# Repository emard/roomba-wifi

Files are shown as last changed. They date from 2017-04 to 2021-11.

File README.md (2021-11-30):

# WiFi-Roomba: ESP8266 Nodemcu interface for iRobot Roomba

Wifi remote control interface for the iRobot Roomba vacuum cleaner.
Tested on model 880, others 600-900 have similar command
set and probably will work too.

telnet to roomba IP while it is charging, it should display something like this:

    telnet 192.168.0.2
    Trying 192.168.0.2...
    Connected to 192.168.0.2.
    Escape character is '^]'.
    bat:   min 0  sec 10  mV 17061  mA 1016  tenths-deg-C 348  mAH 2696  state 5  
    bat:   min 0  sec 11  mV 17061  mA 1016  tenths-deg-C 348  mAH 2696  state 5  
    bat:   min 0  sec 12  mV 17061  mA 1008  tenths-deg-C 348  mAH 2696  state 5  
    bat:   min 0  sec 13  mV 17061  mA 1023  tenths-deg-C 348  mAH 2696  state 5  

To reset roomba to similar state like battery was replaced,
type CTRL-G and ENTER. Roomba beeps and prints different
messages after reset and again battery charging messages as above.

to exit telnet, type CTRL-] quit ENTER

    ^]
    telnet> quit

python3 script to send "DOCK" command

    #!/usr/bin/env python3
    import socket
    s = socket.socket(socket.AF_INET, socket.SOCK_STREAM)
    s.connect(("192.168.0.2",23))
    #print(s.recv(256))
    #s.send(bytearray([128, 135, 173])) # start, clean, stop
    s.send(bytearray([128, 143, 173])) # start, seek dock, stop
    s.close()

python3 script to shown 4 chars approximated on 7-segment display:

    #!/usr/bin/env python3
    import socket, sys, time
    disp = sys.argv[1][0:4].encode() # max 4 chars
    disp += b" " * (4-len(disp)) # pad length 4 with spaces
    s = socket.socket(socket.AF_INET, socket.SOCK_STREAM)
    s.connect(("192.168.48.116",23))
    s.send(bytearray([128, 131, 174])) # safe mode
    time.sleep(0.05)
    s.send(bytearray([164])+disp)
    s.close()

    ./roomba.disp.py TEST

Other commands are described in
[iRobot Roomba 600 Open Interface Spec](https://www.irobotweb.com/-/media/MainSite/PDFs/About/STEM/Create/iRobot_Roomba_600_Open_Interface_Spec.pdf)

# Wifi Module

Get nodemcu from ebay for $3.5 and flash it with some TCP-serial
bridge code.

From Arduino install ESP8266 support from Boards Manager.

set board to "NodeMCU 1.0 (ESP-12E Module)".

open Examples -> ESP8266Wifi ->  WifiTelnetToSerial

setup WiFi user and password to connect to local access 
point and enable "SWAP_PINS" to use hardware serial 115200,8,n,1
connected as RX=gpio13, TX=gpio15 to Roomba:

    #define SWAP_PINS 1

To compile and write flash, click round blue button with right arrow.

When monitored at USB-serial port, it will print IP address where it
connected.

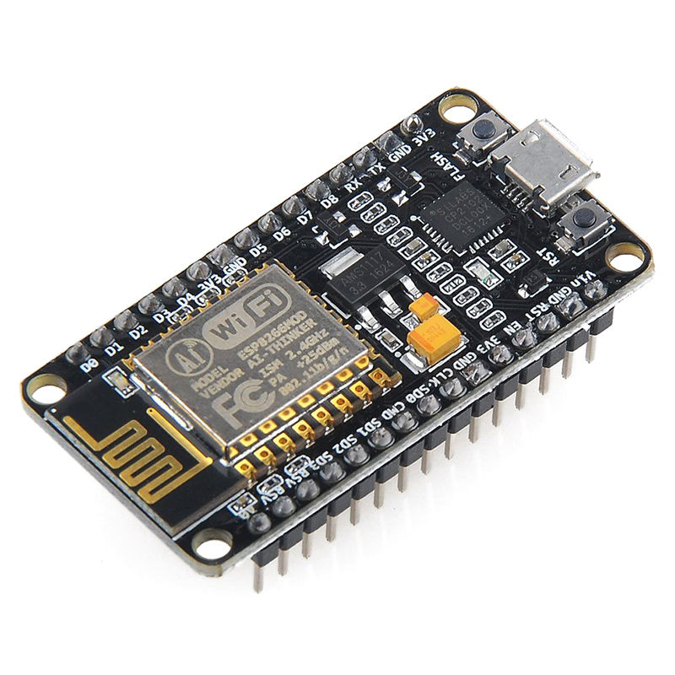
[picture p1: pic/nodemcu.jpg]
nodemcu


# Power supply

Get 3.3V switching power supply module from ebay for $2:

    2A DC 5V-23V to 3.3V DC-DC Step-Down Power Supply Buck Module for esp8266 WiFi

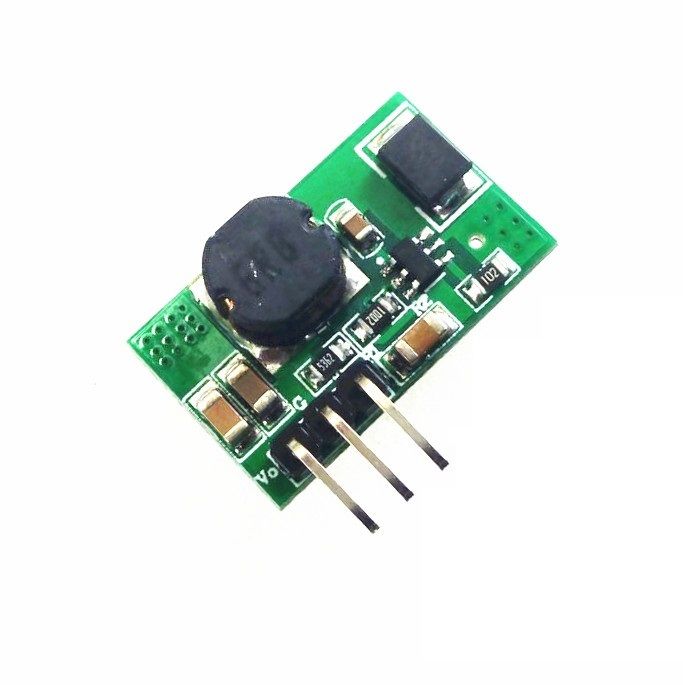
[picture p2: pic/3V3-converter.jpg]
3.3V converter


On the back of the module PCB is written:

       Canton-Power
          DC-DC
    Step-Down Converter
    3.3V[x] 5V[ ] Vi GND Vo

# Cable

Adafruit has roomba cable.
Also apple or mac 8-pin mini-din cable ordered from ebay
will fit to roomba socket (it has extra middle pin which
is NC in roomba socket).

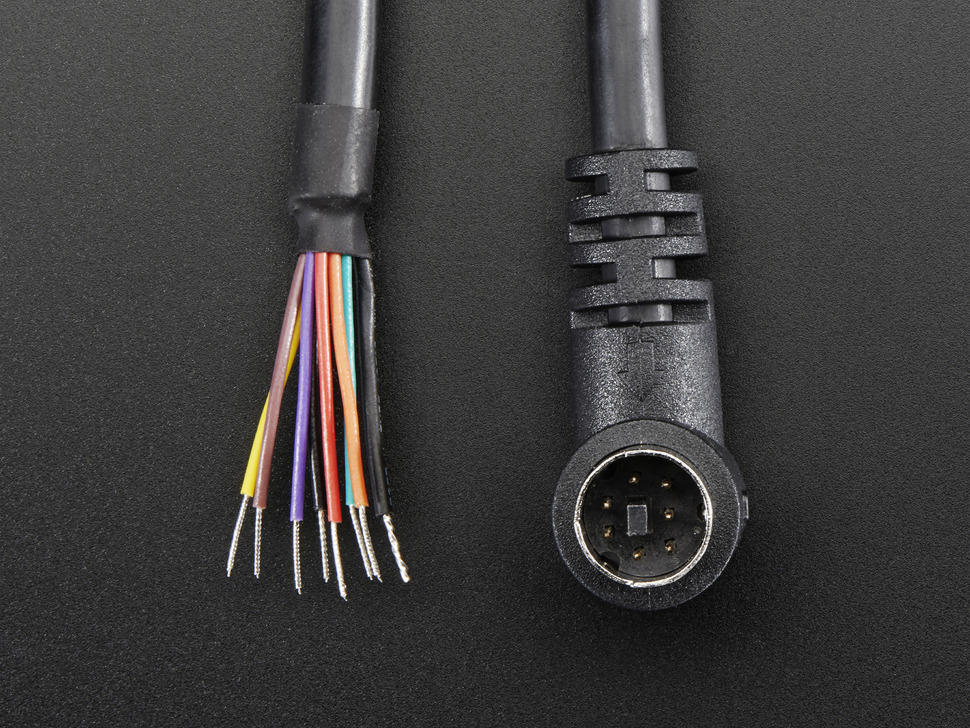
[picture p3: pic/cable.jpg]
cable


pinout (wire colors inside of apple cable)

    1  Vpwr   red    ? no voltage
    2  Vpwr   brown  20V
    3  RXD    orange input to roomba 5V TTL <- wifi_gpio15
    4  TXD    black  output from roomba 5V TTL -> wifi_gpio13
    5  DD     yellow wifi_gpio12
    6  GND    green
    7  GND    blue
    8  NC     violet (middle pin)
    SHIELD    naked

same pin numbering to DB9 connector

# PCB

You can order from OSHpark, seeedstudio or similar, email them gerber
files and they will send back the PCB:

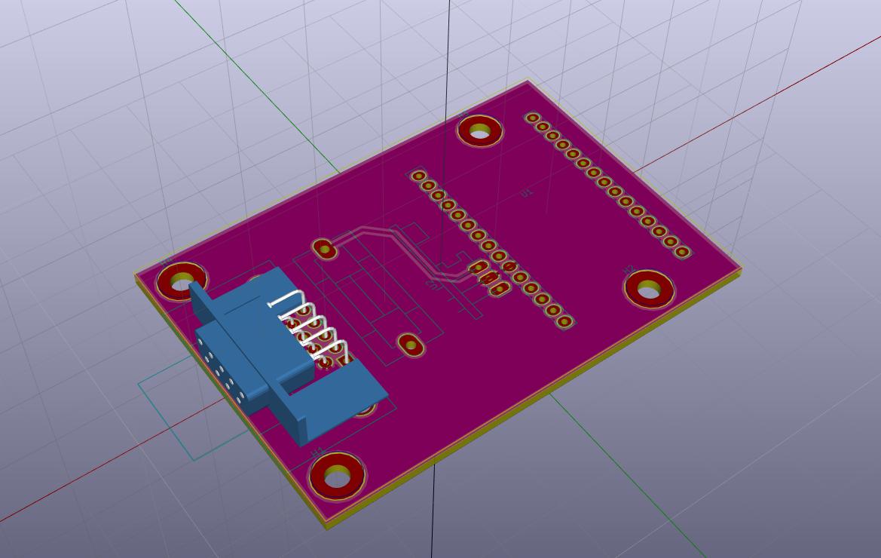
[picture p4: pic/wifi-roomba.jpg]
pcb


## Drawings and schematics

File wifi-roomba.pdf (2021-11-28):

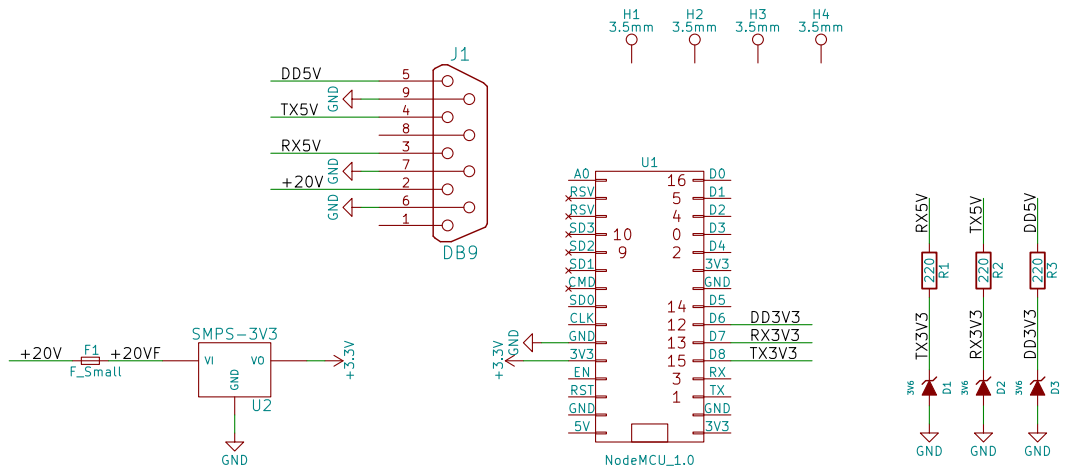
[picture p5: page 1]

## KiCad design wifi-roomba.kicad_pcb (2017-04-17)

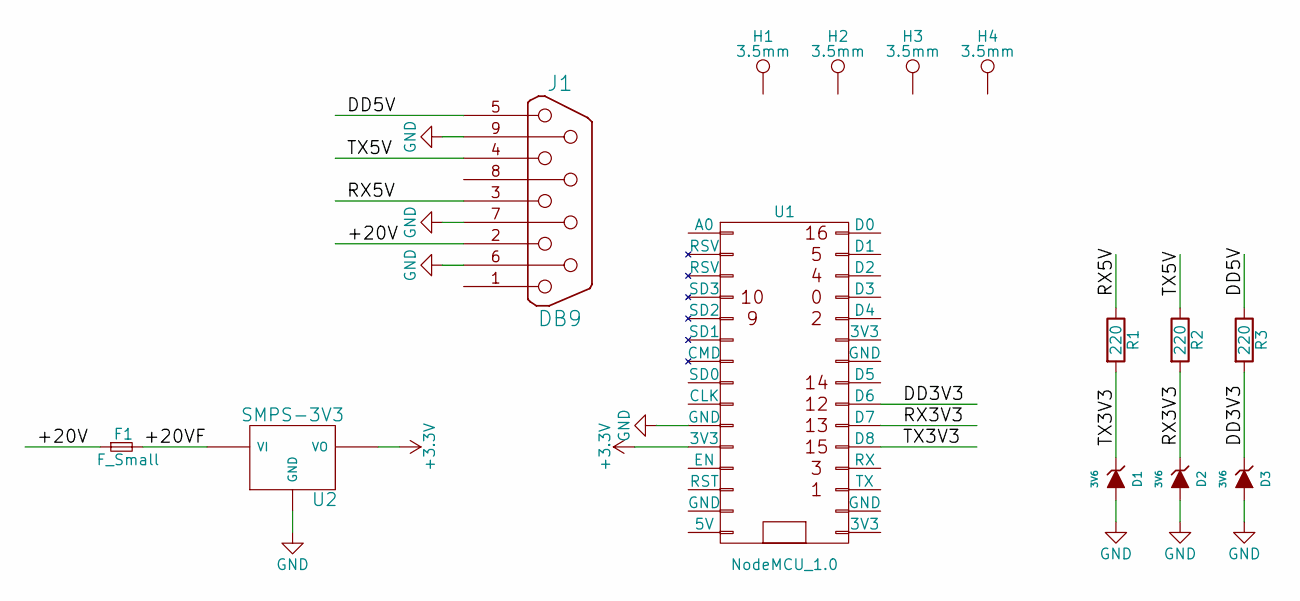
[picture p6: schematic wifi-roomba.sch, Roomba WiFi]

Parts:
D1, D2, D3: 3V6; SMD-1206_Pol
F1: F_Small; Fuseholder5x20_horiz_SemiClosed_Casing10x25mm
H1, H2, H3, H4: 3.5mm; MountingHole_3.5mm_Pad
J1: DB9; DB9FC
R1, R2, R3: 220; R_1206
U1: NodeMCU_1.0
U2: SMPS-3V3; PINHEAD1-3

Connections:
+3V3: U1.11 (3V3), U2.VO
/+20V: F1.1, J1.2
/+20VF: F1.2, U2.VI
/DD3V3: D3.1 (K), R3.2, U1.22 (D6)
/DD5V: J1.5, R3.1
/RX3V3: D2.1 (K), R2.2, U1.21 (D7)
/RX5V: J1.3, R1.1
/TX3V3: D1.1 (K), R1.2, U1.20 (D8)
/TX5V: J1.4, R2.1
GND: D1.2 (A), D2.2 (A), D3.2 (A), J1.6, J1.7, J1.9, U1.10 (GND), U2.GND

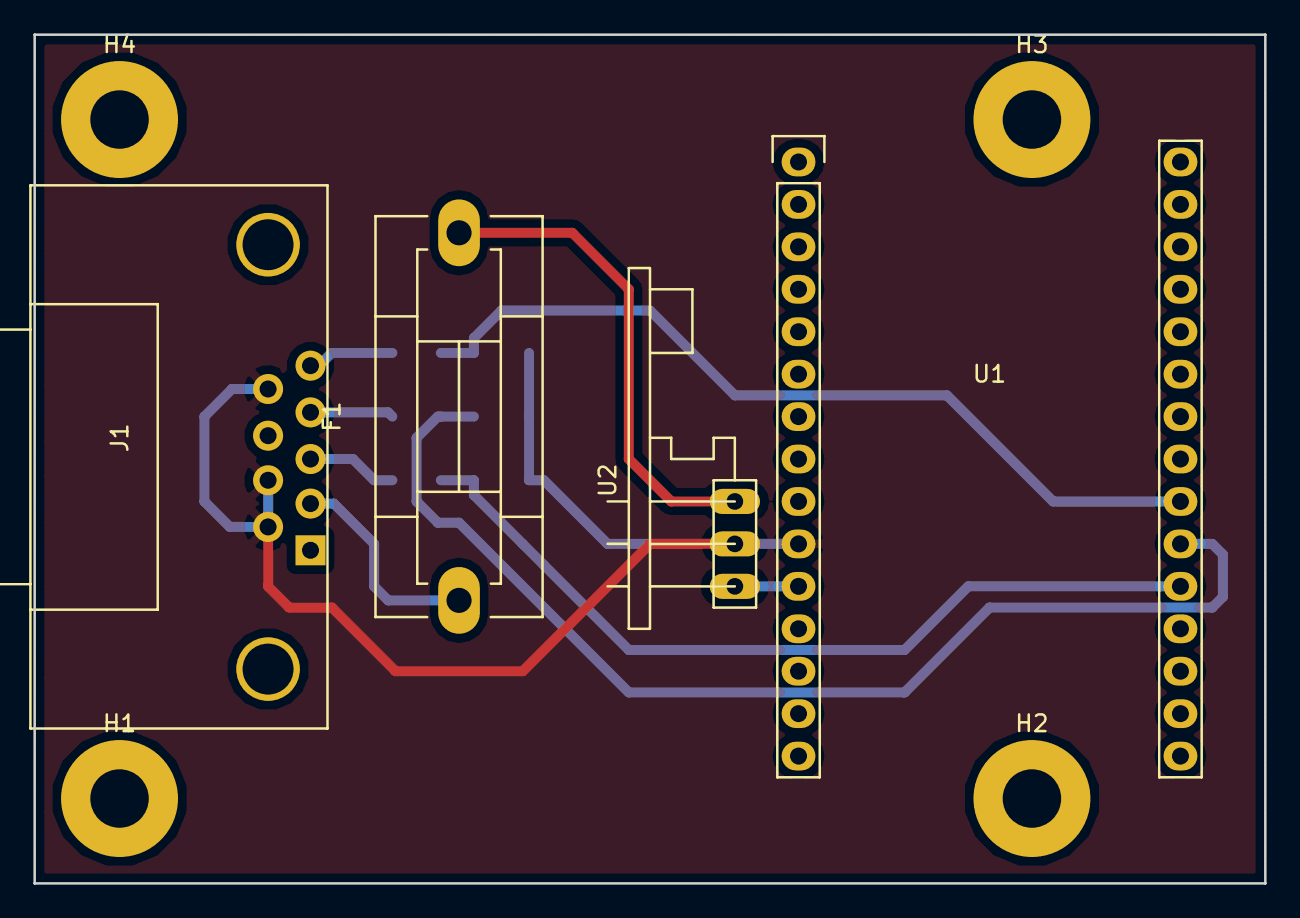
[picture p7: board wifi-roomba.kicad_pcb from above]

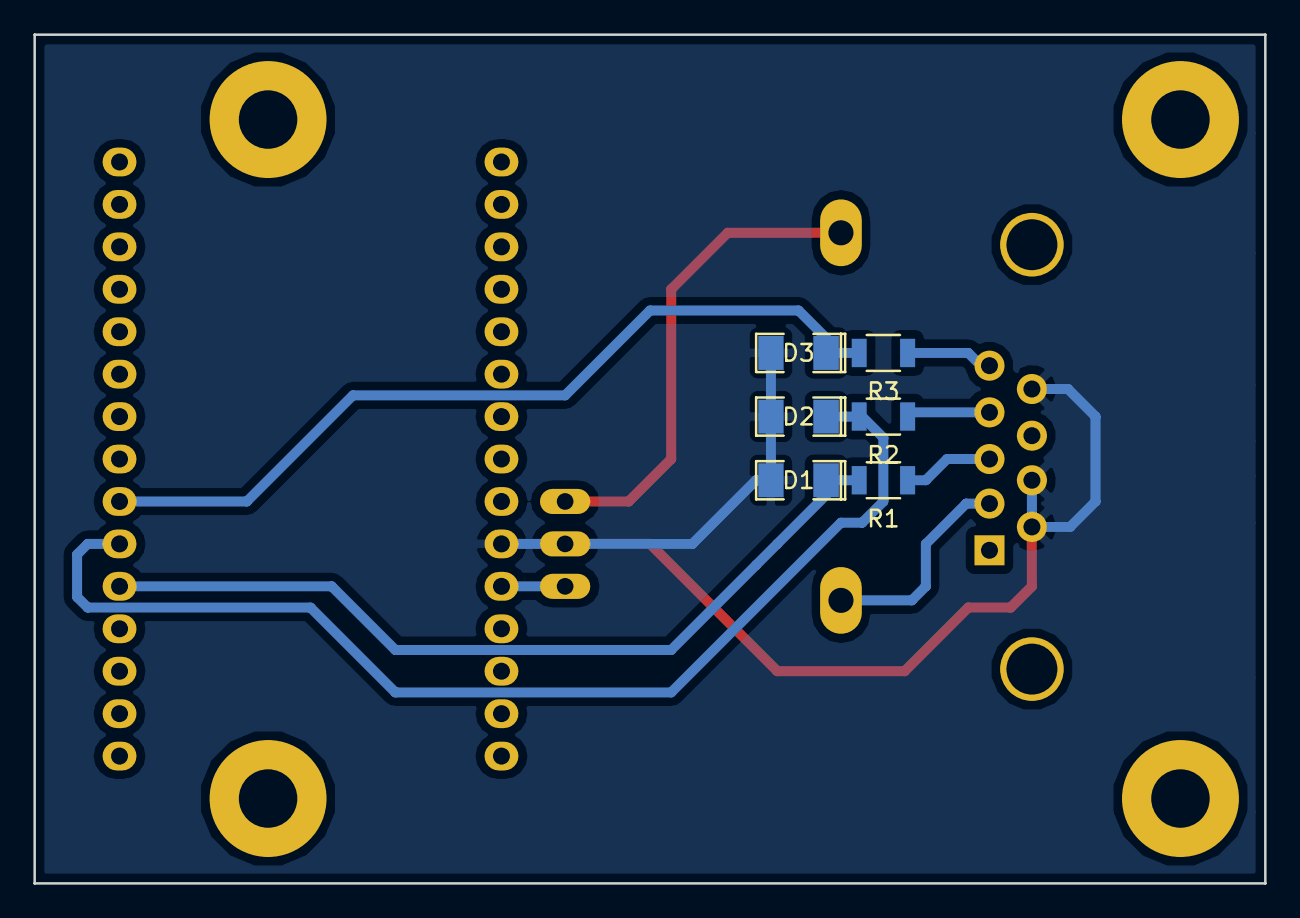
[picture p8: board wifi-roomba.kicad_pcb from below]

Board: 2 copper layers, 73.7 x 50.8 mm, 14 parts (6 on the bottom side), 10 nets.

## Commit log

2017-04-17 readme cable pinout
2017-04-17 readme update, power supply order details
2021-11-28 schematics pdf
2021-11-29 readme what should be printed and how to reset roomba
